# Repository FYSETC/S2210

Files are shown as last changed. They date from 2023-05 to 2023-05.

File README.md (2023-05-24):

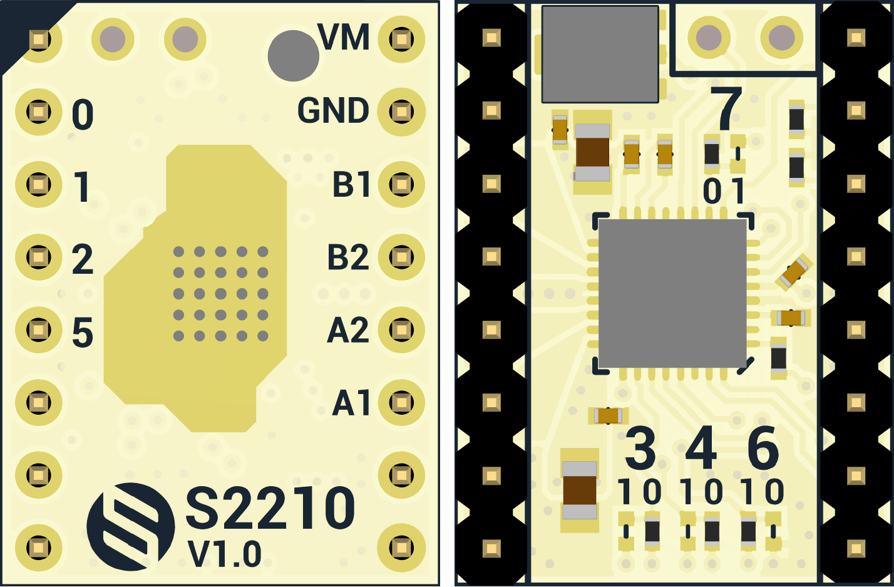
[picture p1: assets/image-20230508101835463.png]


# 1.Product Introduction

The S2210 driver module is designed based on Trinamic's new generation chip TMC2210. Thanks to the brand-new architecture and process, its peak current can reach 3.0A, its continuous current can reach 2.1A, and it can withstand an input voltage up to 36V. TMC2100. All its functions only need to configure the IO hardware, no software programming is required.

# 2.Features

- Hardware compatible with StepStick and Pololu A4988 Stepper Driver
- Components on bottom PCB side for better heat emission
- Automatic standby current reduction
- StealthChop2™ silent PWM mode- for quiet operation and smooth motion
- SpreadCycle - highly dynamic motor control chopper
- Drive capability up to 2.1A (RMS) & 3.0A(PEAK)  coil current
- Step/Dir interface with microstep interpolation (up to 256 microsteps)
- Input microsteps 1-64 optional 
- Configuration via CFG pins
- Supply voltage 4.5-36V

# 3. Specifications Comparison

Model                               |TMC2100|TMC2209|TMC2210
:----:                                     |:----:|------                                     |------                                     
Interface	                    |	Step/Dir| Step/Dir | Step/Dir 
Configuration	|CFG Pins	|UART	|CFG Pins	
Native Microsteps|up to 1 ⁄ 16|up to 1 ⁄ 32|up to 1 ⁄ 64
microPlyer Microsteps| 1 ⁄ 256 | 1 ⁄ 256 | 1 ⁄ 256 
Logic Supply Voltage (VIO)| 3.0 - 5.25V | 3 - 5.25V | 2.2 - 5V 
Motor Supply Voltage (VM)|	4.75 - 46V	|	4.75 - 28V	|	4.5 - 36V	
Motor Phase Current max|	1.2A RMS, 1.7A Peak	|	2A RMS, 2.8A Peak	|	2.1A RMS, 3.0A Peak	
Internal V-  Regulator|	enabled| enabled | enabled 
RDSon (typ. at 25°C)|LS 400mΩ & HS 500mΩ|170mΩ|230mΩ
Rsence|0.11Ω|0.11Ω|chip built-in
stealthChop (quiet)|	yes| yes | yes 
spreadCycle|	yes| yes | yes 
coolStep | no| yes | no 
stallGuard | no| yes | no 
dcStep | no| yes | no 

# 4. Pin Functions

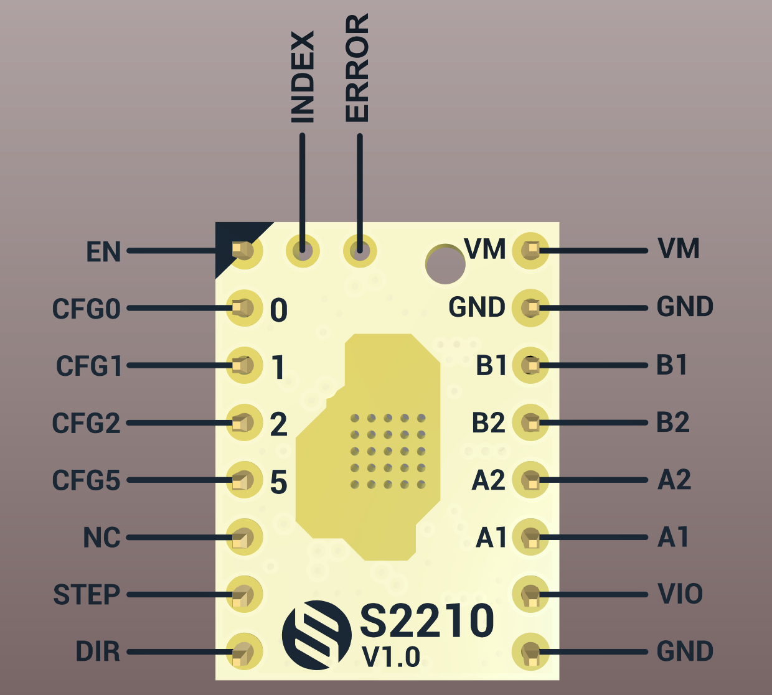
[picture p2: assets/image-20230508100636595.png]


Pin|Function
:----:|----
 &nbsp;|**Power Supply**
 GND|	Ground
VM|	Motor Supply Voltage
VIO	|Logic Supply Voltage
 &nbsp;|**Motor Outputs**
B1|	Motor Coil 1
B2	|Motor Coil 1
A2|	Motor Coil 2
A1	|Motor Coil 2
 &nbsp;|**Control Inputs**
STEP	|Step-Signal Input
DIR	|Direction-Signal Input
 &nbsp;|**CFG Pins**
EN	|Enable Motor Outputs: GND=on, VIO=off, OPEN=Auto-Power-Down
CFG0	|Onboard pulled down，CONFIGURATION OF MICROSTEP RESOLUTION FOR STEP INPUT
CFG1	|Onboard pulled down， CONFIGURATION OF MICROSTEP RESOLUTION FOR STEP INPUT
CFG2	|Chip internal pull-up，CONFIGURATION OF RUN CURRENT IRUN (ALONG WITH IREF RESISTOR), DO NOT CHANGE DURING OPERATION
CFG5	|Chip internal pull-up，SELECTION OF CHOPPER MODE
Index	|Open drain index pulse output indicating, microstep 0 position of coil B.
Error	|Open-drain error output. Use external pullup resistor.<br/>In system reset state, this pin is actively pulled low to indicate reset condition to external controller.
NC	|No pins connected
&nbsp;	|**Onboard Jumper**
CFG3	|Onboard pulled down，CONFIGURATION OF RUN CURRENT IRUN (ALONG WITH IREF RESISTOR), DO NOT CHANGE DURING OPERATION
CFG4	|Onboard pulled down，DIGITAL CURRENT SCALE (MAY BE CHANGED DURING OPERATION)
CFG6	|Onboard pulled up，CONFIGURATION OF HOLD CURRENT REDUCTION
CFG7	|Onboard pulled down，CONFIGURATION OF HOLD CURRENT REDUCTION

# 5. Interface Resources

##  Wiring Diagram

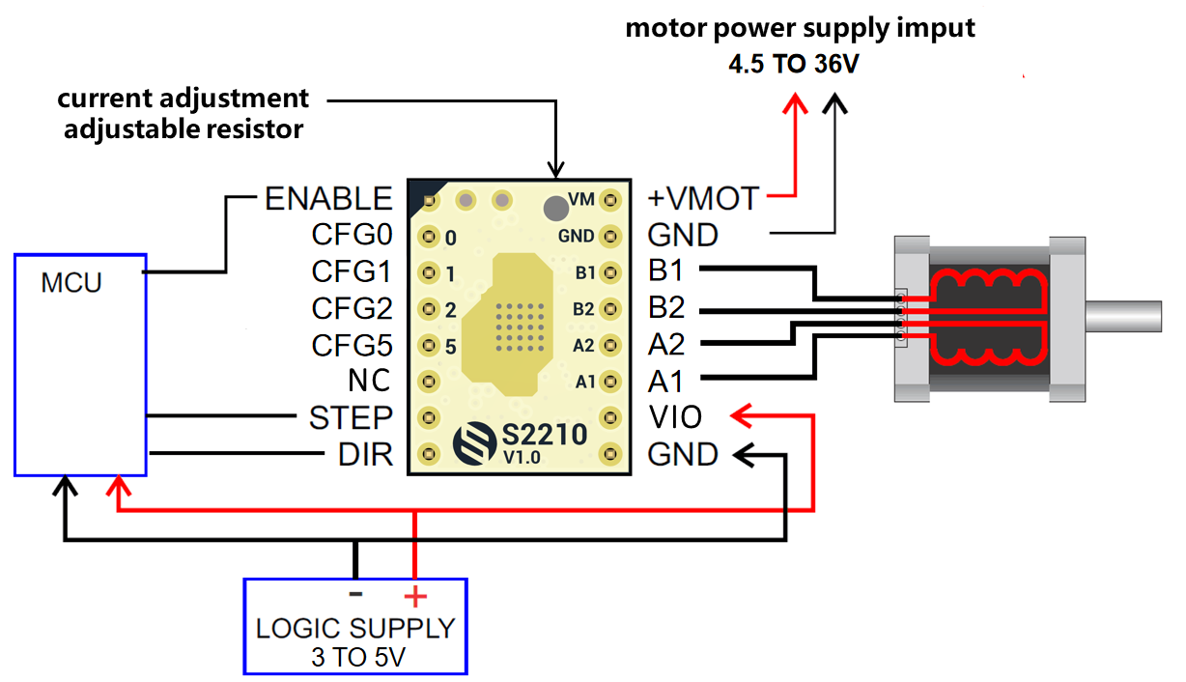
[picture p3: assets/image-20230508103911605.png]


## 5.1 Motor Current Setting

The current setting method of TMC2210 is slightly different, which is determined by CFG2 and CFG3 and the resistance value connected to IREF. Before we start, we need to clarify several relationships:

- IRUN: The current when the motor rotates, set by CFG2 and CFG3 and the resistance value connected to IREF.
- IHOLD: The current at which the motor is held still, set by CFG6 and CFG7.
- IPEAK: Also known as Imax or Full Scale Current, the driver chip provides peak current (the peak value of the sine wave)
- IRMS: The effective value of the current provided by the driver chip (the effective value of the sine wave, usually is about the peak value/1.41)

### 5.1.1. Setting the Full Scale Current Range
The full scale current IFS is a peak current setting. It is selected with an external reference resistor and the two configuration pins CFG2 and CFG3 

Three different full-scale current ranges can be configured through the pins with the same reference resistor to adapt to different motor sizes and applications. This is needed to benefit from the best possible current control resolution. 

Connect a reference resistor RREF from IREF to GND. Together with pins CFG3 and CFG2, the full scale current range IFS is set based on the external resistor . 

The equation below shows the full-scale current IFS as a function of the RREF shunt resistor connected to pin IREF and the configuration pin setting. The proportionality constant KIFS is defined by the CFG2 and CFG3 setting. The external resistor RREF can range between 12kΩ and 60kΩ.

$$
I_{FS}=K_{IFS}(KV)/R_{REF}(kΩ)
$$

Table 9. IFS Full Scale Current Range Settings (Example for RREF = 12KΩ)

| PIN CONFIG IN STANDALONE MODE | PIN CONFIG IN STANDALONE MODE | KIFS (A x kΩ) | MAX FS SETTING | TYPICAL RDS(ON) (HS + LS) | NOTES |
| --- | --- | --- | --- | --- | --- |
| 1 | 1 | 36 | 3A | 0.23Ω | Optimized efficiency for motors and applications rated up to 2.1A rms |
| 1 | 0 | 36 | 3A | 0.23Ω | Optimized efficiency for motors and applications rated up to 2.1A rms |
| *0* | *1* | *24* | *2A* | *0.27Ω* | *Optimized efficiency for motors and applications rated up to 1.4A rms* |
| 0 | 0 | 11.75 | 1A | 0.40Ω | Optimized efficiency for motors and applications rated up to 0.7A rms |
### 5.1.2. Setting the Rref

IFS Full Scale RMS Current in Ampere (A RMS) based on CFG2/CFG3 Pin Settings and different RREF
| RREF(kΩ) | KIFS = 24 |
| --- | --- |
| 12 | 1.41 |
| 15 | 1.13 |
| 18 | 0.94 |
| 22 | 0.77 |
| 27 | 0.63 |
| 33 | 0.51 |
| 39 | 0.44 |
| 47 | 0.36 |
| 56 | 0.30 |

**According to the circuit of the module, we perform this demonstration calculation:**
Rref: The resistor connected to the IREF pin, which consists of a 12K resistor and a maximum 50K adjustable resistor. The factory value of the adjustable resistor is generally located in the center, which is 25K, and all default Rref=37K.
CFG3 is pulled down by default, which is equivalent to the GND level, and CFG2 is high when no external level is connected, so the default KIFS=24KV. 

$$
I_{FS}=K_{IFS}(KV)/R_{REF}(kΩ)=24(KV)/37(KΩ)=0.65A
$$

### 5.1.3 Hold Current (IHOLD) Reduction Configuration

<font color="red">CFG7（**Onboard pulled down**）/CFG6（**Onboard pulled up**）</font>: CONFIGURATION OF HOLD CURRENT REDUCTION

CFG7| CFG6 |HOLD CURRENT REDUCTION
:----:|:----:|:----:
GND |GND |No hold current reduction. IHOLD = IRUN
GND |VCC_IO| Reduction to 50%. IHOLD = 1/2 IRUN
VCC_IO |GND| Reduction to 25%. IHOLD = 1/4 IRUN
VCC_IO |VCC_IO| Reduction to 12.5%. IHOLD = 1/8 IRUN

### 5.1.4 Digital Current Scale Configuration

<font color="red">CFG4（**Onboard pulled down** ）</font>: DIGITAL CURRENT SCALE (MAY BE CHANGED DURING OPERATION)

CFG4 |CURRENT SCALE
:----:|:----:
GND| I = 75% of full scale current IRUN
VCC_IO| I = 100% of full scale current IRUN

## 5.3 Microsteps Setting

Microsteps Resolution Configuration for the Step Input，<font color="red">CFG1（**Onboard pulled down** ）CFG1（**Onboard pulled down** ）</font>，So the default is 8 microsteps.

CFG1|CFG0| microsteps |Interpolation|Mode
:----:|:----:|:----:|:----:|:----:
GND	|GND	|8| 256 | StealthChop2 
GND	|VIO| 16 | 256 | StealthChop2 
VIO|	GND| 32 | 256 | StealthChop2 
VIO	|VIO	|  64   | 256 | StealthChop2 

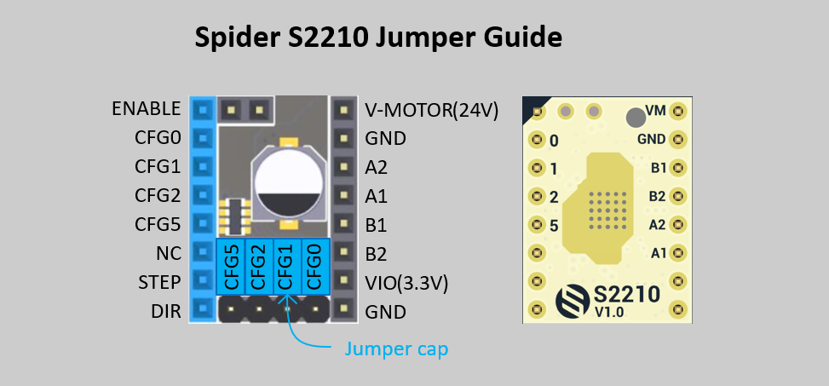
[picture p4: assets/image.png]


# 6. Other Configs 

## 6.1 Chopper Mode Selection
<font color="red">CFG5 **（Chip internal pull-up）**</font>: SELECTION OF CHOPPER MODE

CFG5 | CHOPPER MODE
:----:|:----:
GND | SpreadCycle operation
VCC_IO |StealthChop2 operation

# 7. How to config the code in klipper/marlin

S2210 only needs to configure the corresponding STEP, DIR, EN pins on the software, no additional configuration is required.
It is worth noting that the subdivision parameters on the software need to be consistent with the jumpers on the hardware.

For example, the X-axis configuration in klipper is as follows:

```c++
[stepper_x]
##	Connected to X-MOT (B Motor)
step_pin: PE11
dir_pin: PE10
enable_pin: !PE9
rotation_distance: 40
microsteps: 8
full_steps_per_rotation:200  #set to 400 for 0.9 degree stepper
endstop_pin: ^PB14
position_min: 0

##--------------------------------------------------------------------
position_endstop: 300
position_max: 300
##--------------------------------------------------------------------
homing_speed: 25   #Max 100
homing_retract_dist: 5
homing_positive_dir: true
```

Any configuration such as [tmc2209 stepper_x] is no longer needed.

## NOTE：

1. <font color="red">**Pay attention to the direction.**</font>
2. The heat sink is directly attached to the PCB.
3. The motor direction is the opposite of 4988 and 8825. If you want to replace the 4988 directly, please adjust the firmware or adjust the motor connection.

# Documents

SCH: https://github.com/FYSETC/S2210/blob/main/TMC2210%20V10.pdf

Datasheet: https://www.trinamic.com/fileadmin/assets/Products/ICs_Documents/TMC2210_V10_SCH.pdf

## Shop

- 

## Tech Support

Please submit any technical issue into our [forum](http://forum.fysetc.com/)

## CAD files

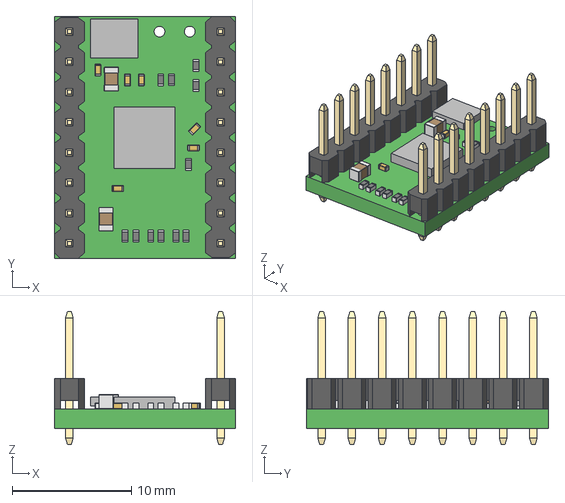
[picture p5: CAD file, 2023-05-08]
TMC2210_V10.step
15.2 x 20.3 x 11.2 mm

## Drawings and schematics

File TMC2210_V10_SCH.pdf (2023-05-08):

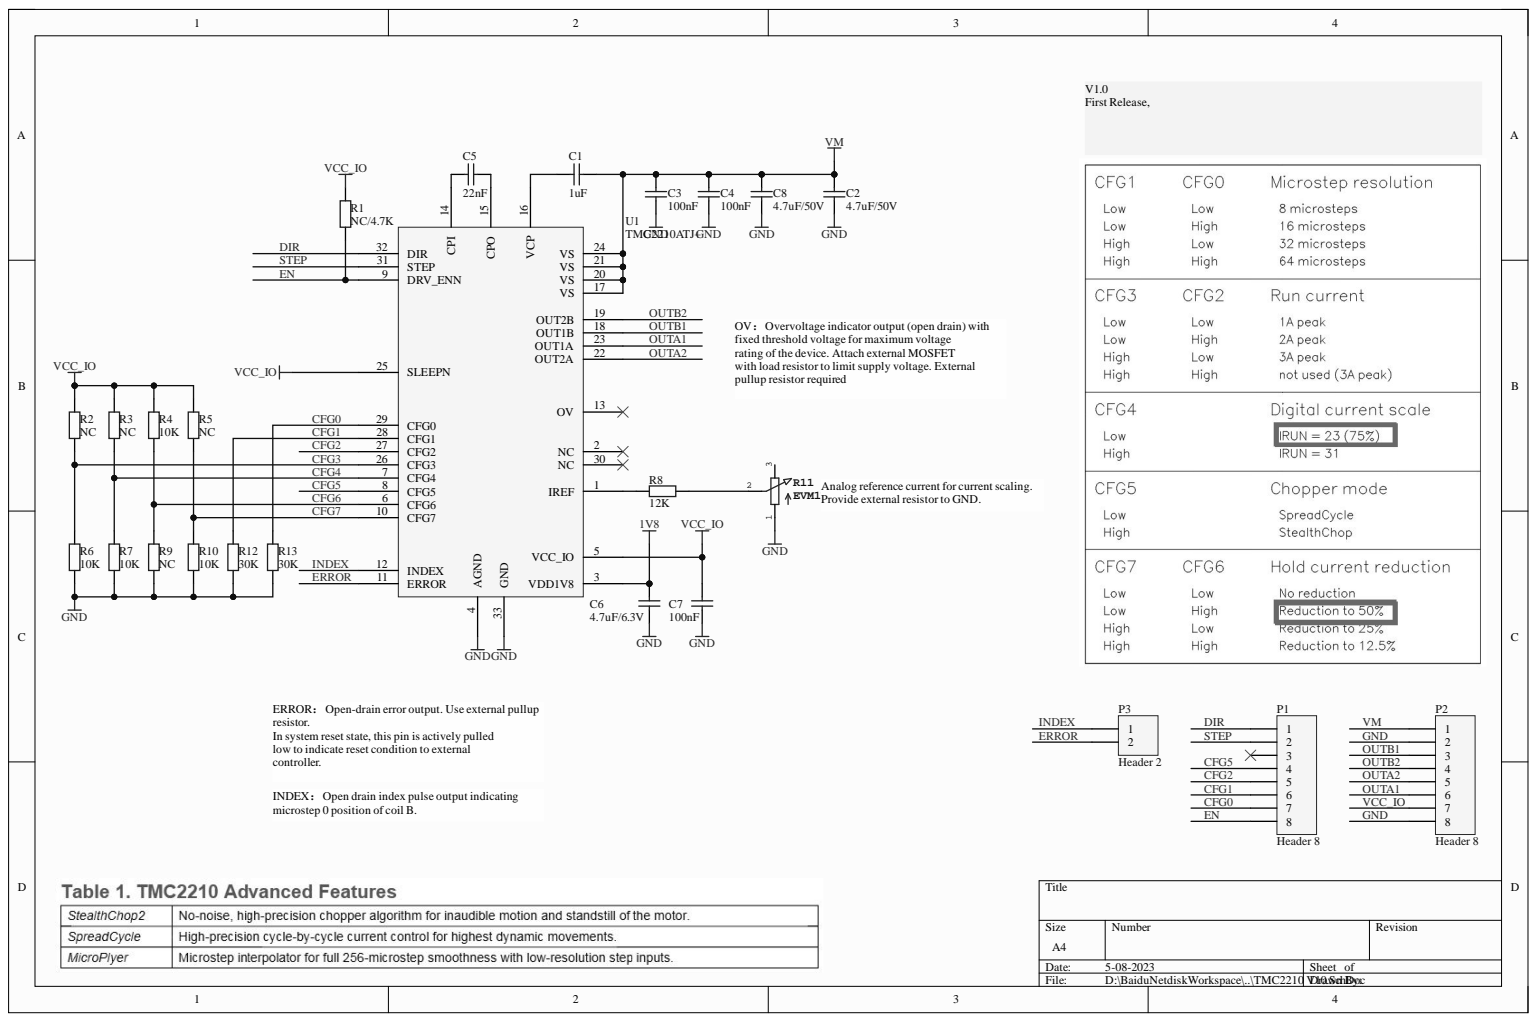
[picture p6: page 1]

CFG 1 | 2
CFG 2 CFG 3 | 2 2

CFG 4 | 7
